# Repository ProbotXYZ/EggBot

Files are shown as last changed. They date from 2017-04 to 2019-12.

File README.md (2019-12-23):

# Egg Painter Mini (eggbot pro MOD)

<p align="center">
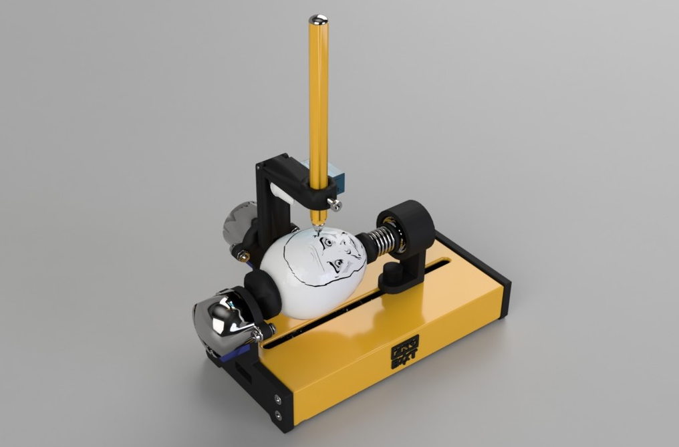
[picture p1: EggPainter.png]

<div align="center"><i>This is a low-cost version of <a href="http://egg-bot.com/">EggBot</a>, printable 3D printers that accept large.</i></div>
</p>  

<a href="https://github.com/ProbotXYZ/EggBot/blob/master/README_RU.md">На Русском</a>

Links
-------------------
<a href="https://www.youtube.com/watch?v=U3JV1u7KEp0"  target="_blank">Video Assembly Instruction</a><br/>
<a href="https://youtu.be/MZZwDX_0e_o"  target="_blank">Video First Launch</a><br/>
<a href="http://www.thingiverse.com/thing:2245428" target="_blank">Thingiverse.com</a><br/>
<a href="http://probot.xyz" target="_blank">Probot.XYZ</a><br/>
<a href="http://egg-bot.com/" target="_blank">Original EggBot</a>

Assembly kits
-------------------
You can buy a complete assembly kit - <a href="http://canbemake.ru/recommends/complete-assembly-kit/">this</a>.

Read this, it's important!
-------------------

If you are reading this, then you may be looking at the development version of EggBot Pro Mini. This means files may present inconsistencies (dimensions mismatch, lack of tolerances, etc). If you just want to build the machine, take a look at the following locations - <a href="https://github.com/ProbotXYZ/EggBot/releases">Releases</a>

The list of parts to print
-------------------
<p align="center">
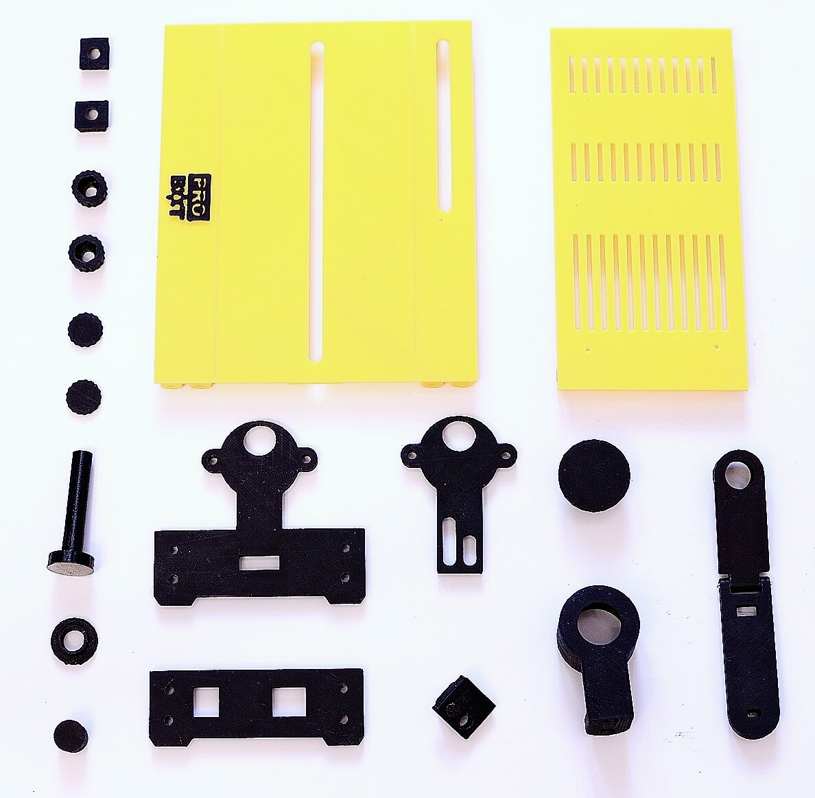
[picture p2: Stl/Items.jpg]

</p>  
1 x 0000001. Case_Bottom<br/>
1 x 0000002. Case_Top<br/>
1 x 0000003. Logo<br/>
2 x 0000004. M4_Nut_Holder<br/>
1 x 0000005. Axis_R<br/>
1 x 0000006. Spring_Holder<br/>
1 x 0000007. Axis_R_Holder<br/>
1 x 0000008. Axis_R_Lock<br/>
2 x 0000009. М4_Bolt_Holder_Bottom<br/>
2 x 0000010. М4_Bolt_Holder_Top<br/>
1 x 0000011. Axis_L_Holder<br/>
1 x 0000012. Axis_L<br/>
1 x 0000013. Hand_Holder<br/>
1 x 0000014. Hand_Holder_Guide<br/>
1 x 0000015. Hand_Holder_Guide_Case<br/>
1 x 0000016. Hand_H<br/>
1 x 0000017. Hand_V<br/>
1 x 0000018. Case_Right<br/>
<br/> 
Download and print all parts - <a href="https://github.com/ProbotXYZ/EggBot/tree/master/Stl/en">this</a><br/> or buy - <a href="http://canbemake.ru/recommends/plastic-parts-ebay/">this</a>.

Non-printable parts
-------------------
2 x <a href="http://canbemake.ru/recommends/608zz-podshipnik/" target="_blank">608zz Bearing</a><br/>
1 x <a href="http://canbemake.ru/recommends/rubber-gasket/" target="_blank">24mm Silicone or Rubber Gasket</a><br/>
1 x <a href="http://canbemake.ru/recommends/rubber-gasket/" target="_blank">15mm Silicone or Rubber Gasket</a><br/>

Screws&Nuts
-------------------
1 x <a href="http://canbemake.ru/recommends/pruzhiny/" target="_blank">Spring Diameter 9-15mm Length 17-20mm</a><br/>
1 x 2x18mm Iron Nail without a hat or <a href="http://canbemake.ru/recommends/zaklepka/" target="_blank">Rivet</a><br/>
2 x <a href="http://canbemake.ru/recommends/m5x20/" target="_blank">M5x20 Bolt</a><br/>
2 x <a href="http://canbemake.ru/recommends/m5-nut/" target="_blank">M5 Nut</a><br/>
8 x <a href="http://canbemake.ru/recommends/komplekt-boltov-m3/" target="_blank">M3x12 Screw</a><br/>
5 x <a href="http://canbemake.ru/recommends/komplekt-boltov-m3/" target="_blank">M3x16 Screw</a><br/>
12 x <a href="http://canbemake.ru/recommends/komplekt-boltov-m3/" target="_blank">M3 Nut</a><br/>
4 x <a href="http://canbemake.ru/recommends/komplekt-boltov-m3/" target="_blank">M3 Washer</a><br/>
12 x <a href="http://canbemake.ru/recommends/m2x4/" target="_blank">M2x4 or M2x5 Screw</a><br/>

Electronics
-------------------
1 x <a href="http://canbemake.ru/recommends/arduino-uno/" target="_blank">Arduino UNO</a><br/>
2 x <a href="http://canbemake.ru/recommends/uln2003-drajver-shagovogo-dvigatelya/" target="_blank">ULN2003 Stepper Motor Driver Board</a><br/>
2 x <a href="http://canbemake.ru/recommends/28byj-48-12v-shagovyj-dvigatel/" target="_blank">28byj-48-12v Stepper Motor</a><br/>
1 x <a href="http://canbemake.ru/recommends/sg90-mikro-servo-dvigatel/" target="_blank">SG90 Micro Servo</a><br/>
1 x <a href="http://canbemake.ru/recommends/12v-blok-pitaniya/" target="_blank">12V DC Power Supply</a><br/>
1 x <a href="http://canbemake.ru/recommends/usb-kabel-dlya-pk/" target="_blank">USB Cable for connect to PC</a><br/>
<a href="http://canbemake.ru/recommends/nemnogo-provodov/" target="_blank">A few wires</a><br/>

Assembly Instructions
-------------------
<a href="https://www.youtube.com/watch?v=U3JV1u7KEp0"  target="_blank">Video Assembly Instructions</a>.<br/>
Download Assembly Instructions PDF<a href="https://github.com/ProbotXYZ/EggBot/blob/master/AssemblyInstructions/Assembly_Instruction.pdf">this</a>.<br/>
3D model <a href="https://github.com/ProbotXYZ/EggBot/blob/master/AssemblyInstructions/Instruction%203D.stl">this</a>.

<p align="center">
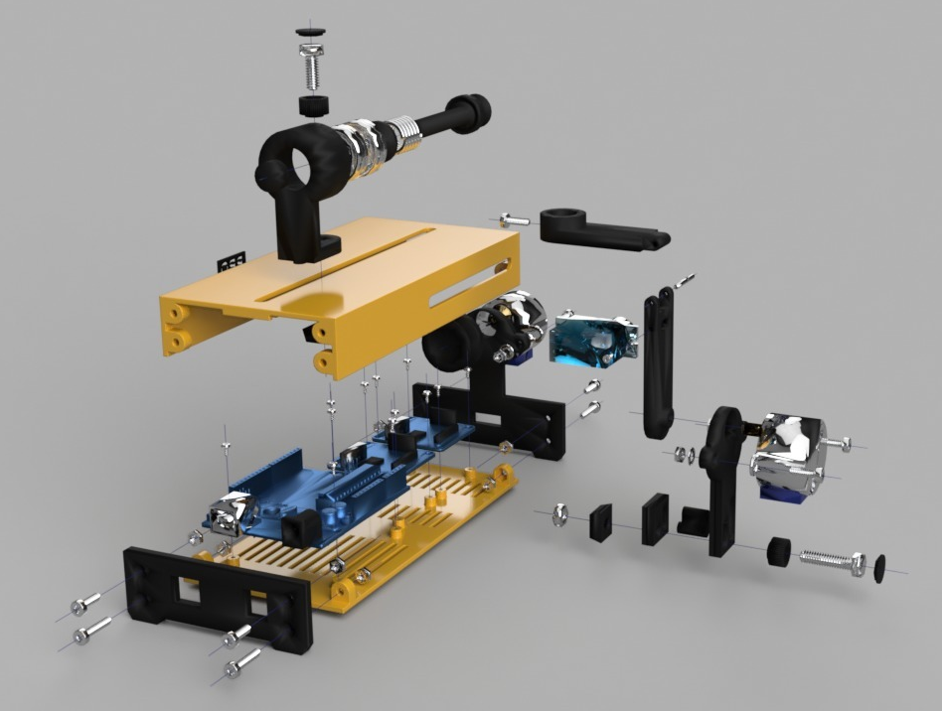
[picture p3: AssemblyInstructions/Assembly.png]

</p>  

Firmware
-------------------
As the firmware used Eggduino. It's arduino firmware for EggBot / Spherebot with Inkscape-Integration (<a href="https://github.com/cocktailyogi/EggDuino">Github</a>).

For Installation:
1) Download and unzip <a href="https://github.com/ProbotXYZ/EggBot/blob/master/Firmware/Firmware.zip">Firmware.zip</a>.
2) For UNO board with CH340G download and install driver: http://www.wch.cn/download/CH341SER_ZIP.html.
3) Download the ARDUINO IDE here: https://www.arduino.cc/en/Main/Software and install it.
4) Run the software. Select the Arduino UNO board and the proper COM PORT (should be COM5 or so) in the menu "Tools->Board"…
5) Open Eggduino.ino from <a href="https://github.com/ProbotXYZ/EggBot/blob/master/Firmware/Firmware.zip">Firmware.zip</a> and upload the Eggduino code to your Arudino Uno. 

Controlling program
-------------------
As the controlling program used Inkscape software.
1) Download and unzip the Inkscape software <a href="https://github.com/ProbotXYZ/EggBot/blob/master/Software/Software_(inkscape%2Bextension).zip">Software_inkscape+extension.zip</a>.
2) EggBot Control Extension already included in the Inkscape from <a href="https://github.com/ProbotXYZ/EggBot/blob/master/Software/Software_(inkscape%2Bextension).zip">Software_inkscape+extension.zip</a>.
3) Run the software. 

The EggBot Control extension for Inkscape is the tool that you will use to help you test and align the EggBot, as well as transfer your drawings to an egg. Once Inkscape is running, you’ll have an Extensions menu, and on that menu will be a submenu labeled Eggbot.

If the Inkscape does not connect to the device, please check name of your Arduino in to device manager. And change it in ebb_serial.py on line 52 instead of "USB-SERIAL CH340":

- open file "ebb_serial.py" in text editor and search for the following block:

    EBBport = None
    for port in comPortsList:
        if port[1].startswith("EiBotBoard"):
            EBBport = port[0]   #Success; EBB found by name match.
            break   #stop searching-- we are done.
    if EBBport is None:
        for port in comPortsList:
            if port[2].startswith("USB VID:PID=04D8:FD92"):
                EBBport = port[0] #Success; EBB found by VID/PID match.
                break   #stop searching-- we are done.      

- replace "04D8:FD92" with the VID/PID of your Arduino device.  

- alternatively, you can replace "EBBport = None" with your specific port number:
    EBBport = "COMxx"               #Windows
    EBBport = "/dev/tty[something]" #Linux/Mac  

Use template EggBot (File->New from Template) for your drawing.

Examples
-------------------
<a href="https://github.com/ProbotXYZ/EggBot/tree/master/Samples">Sample pictures</a>

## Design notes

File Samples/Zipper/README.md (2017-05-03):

# zipper template for eggbot
by schuetzi99

<p align="center">
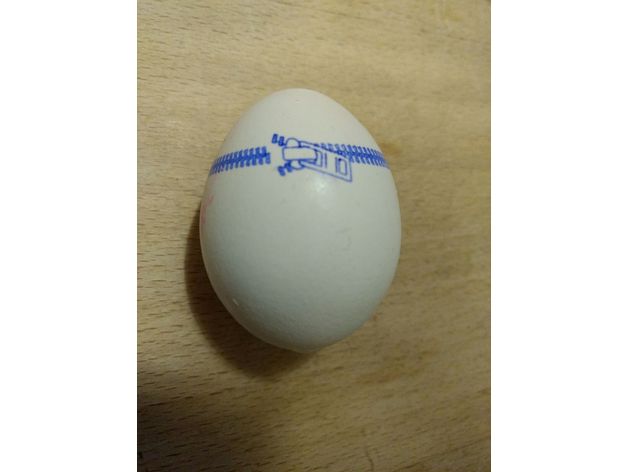
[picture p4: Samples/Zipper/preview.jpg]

</p>

http://www.thingiverse.com/thing:1981701

Summary

This is a template to print an zipper onto a egg.
https://youtu.be/jIhRP3eUceU

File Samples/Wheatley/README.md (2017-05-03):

# Eggbot - Wheatley
by R0b0Genius

http://www.thingiverse.com/thing:84653

Summary

Designed for The Original Egg-Bot Kit.
Colors are Sharpie Ultra Fine unless otherwise noted.

5 Color-Layer Plot
1: Turquoise
2: Navy Blue
3: Slate Gray
4: Black
5: Black (Martha Stewart .1mm)

www.egg-bot.com
www.evilmadscientist.com

Wheatley A© Valve Corporation

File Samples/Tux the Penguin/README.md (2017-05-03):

# Eggbot - Tux the Penguin
by R0b0Genius

<p align="center">
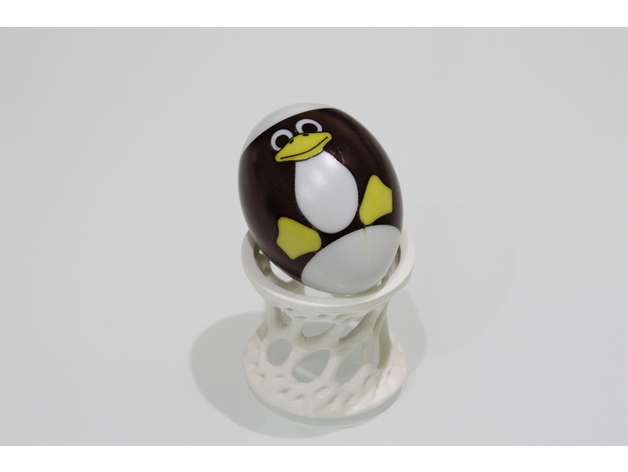
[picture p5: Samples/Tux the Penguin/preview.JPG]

</p>

http://www.thingiverse.com/thing:86924

Summary

Designed for The Original Egg-Bot Kit.
Colors are Sharpie Ultra Fine unless otherwise noted.

3 Color-Layer Plot
1: Leg Warmer Yellow
2: Slate Gray
3: Black

www.egg-bot.com
www.evilmadscientist.com

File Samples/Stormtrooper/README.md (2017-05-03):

# Eggbot - Stormtrooper
by FabLabEP

<p align="center">
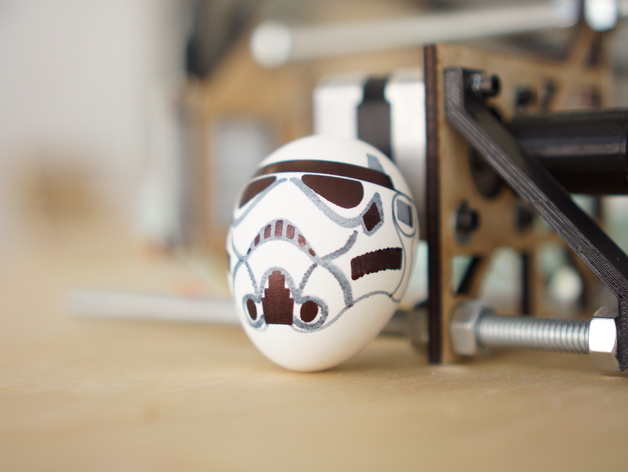
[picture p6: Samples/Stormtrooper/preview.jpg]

</p>

http://www.thingiverse.com/thing:302943

SVG file ready to print on your Eggbot.

Layers:
1: Grey
2: Black

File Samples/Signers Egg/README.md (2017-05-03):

# Signers Egg for Eggbot
by HooDat

<p align="center">
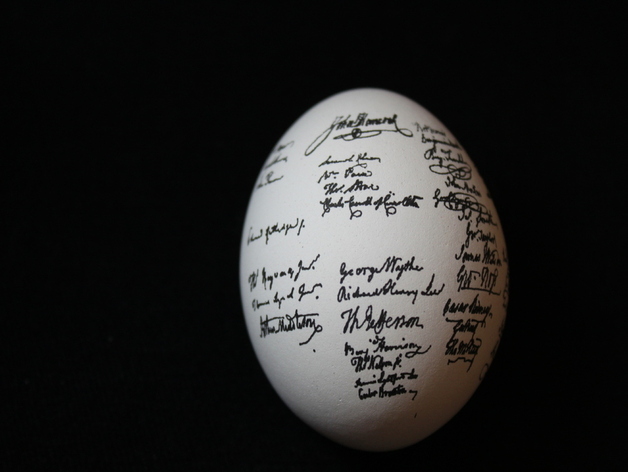
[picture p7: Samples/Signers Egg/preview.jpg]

</p>

http://www.thingiverse.com/thing:18359

Summary

Signers of the Declaration plotted with the Eggbot.
Unable to find a suitable vector based file of the Declaration, I manually traced all 56 Signers in Illustrator, saving them as smoothed paths, then imported the entire document into Inkscape. Most of them follow the pen stroke that the original Signer probably followed in 1776.

Instructions

If plotting on a normal sized egg, use as fine a point as possible. I used a 0.03mm Copic Multiliner for the pictured egg.
On larger eggs (goose, for example) it will plot OK with the .2mm Micron (size 005).

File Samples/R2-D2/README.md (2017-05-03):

# R2-D2 Eggbot Egg
by bfergus

<p align="center">
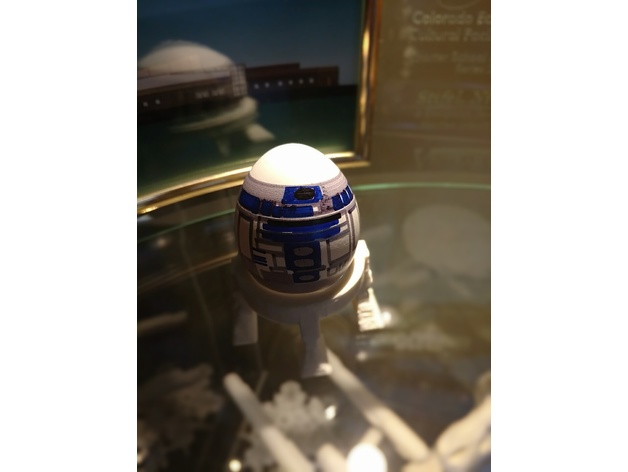
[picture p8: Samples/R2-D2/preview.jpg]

</p>

http://www.thingiverse.com/thing:2233788

Summary

Built this eggbot like this http://www.thingiverse.com/thing:299483. Making eggs. Next logical step- an egg that uses BOTH: the eggbot and printer! Here's a remixed egg stand that mimics R2D2 Legs, and an eggbot pattern for drawing an R2D2 Egg.

How I Designed This

For stand, a remix of a couple models. For the eggbot pattern, downloaded a papercraft R2D2 and converted to a multi layer svg= adding some hatching as appropriate.

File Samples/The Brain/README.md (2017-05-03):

# Eggbot - The Brain
by R0b0Genius

<p align="center">
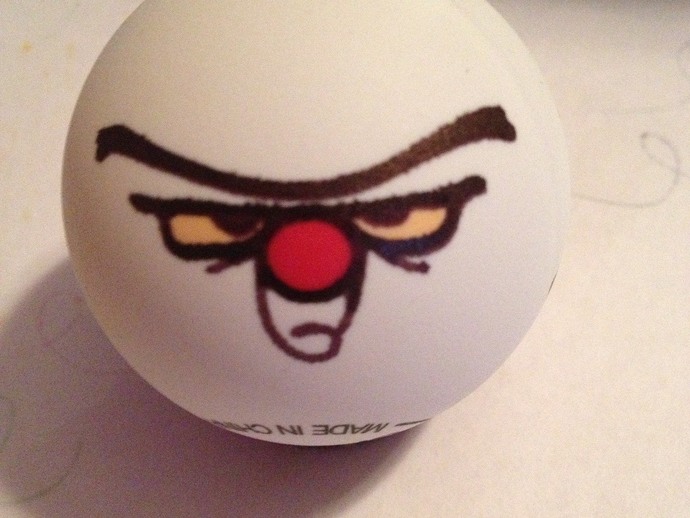
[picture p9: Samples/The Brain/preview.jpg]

</p>

http://www.thingiverse.com/thing:85200

Summary

Designed for The Original Egg-Bot Kit.
Colors are Sharpie Ultra Fine unless otherwise noted.

3 Color-Layer Plot
1: Peach
2: Red
3: Black

www.egg-bot.com
www.evilmadscientist.com

The Brain A© Warner Bros. Entertainment Inc

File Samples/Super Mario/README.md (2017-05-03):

# Super Mario Eggbot Egg
by nebarnix

<p align="center">
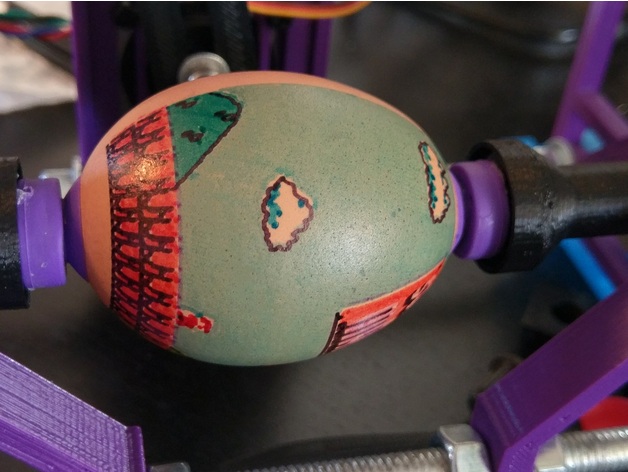
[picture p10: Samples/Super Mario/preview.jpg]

</p>

http://www.thingiverse.com/thing:2095503

Summary

The paths are somewhat messy.... Due to this it takes a while. Feel free to clean up if you have 4 hours of your life you will never get back!

Also, you should probably use a white egg, not a brown one. The sky looks a sickly grey. Maybe its just a winter inversion mario?

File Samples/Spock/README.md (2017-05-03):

# Eggbot Spock
by peterinaz

<p align="center">
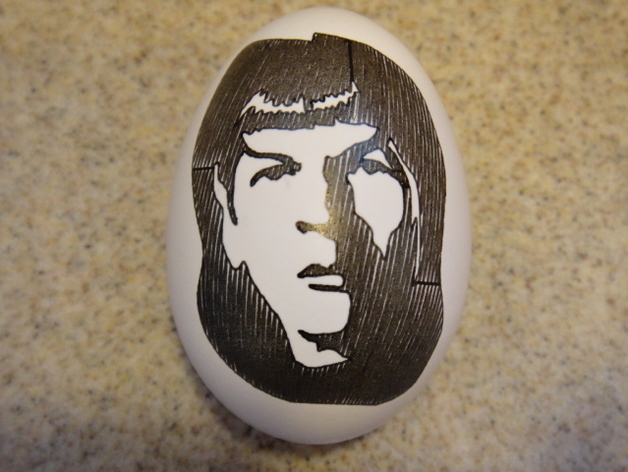
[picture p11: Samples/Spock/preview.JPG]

</p>

http://www.thingiverse.com/thing:1322623

Summary

Is there anything that really needs to be said? Done with a Sakura Pigma Micron .005 pen.

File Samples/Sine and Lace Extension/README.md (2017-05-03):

# Eggbot Sine and Lace Extension
by dnewman

<p align="center">
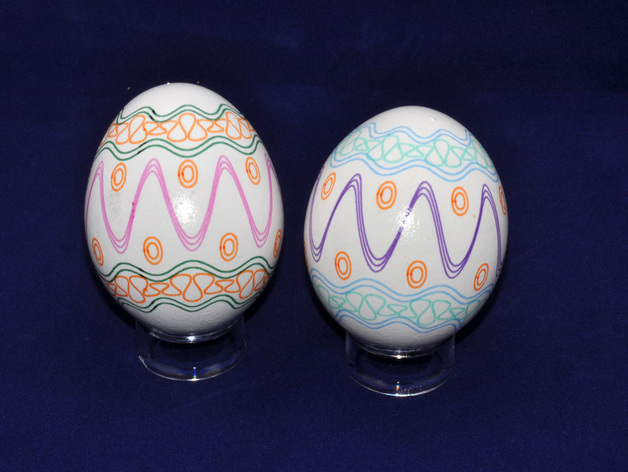
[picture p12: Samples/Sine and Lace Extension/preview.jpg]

</p>

http://www.thingiverse.com/thing:24594

Summary

Sine and Lace is an Inkscape extension intended for use with the Eggbot. It may be used to draw sinusoidal and lace patterns with periods a multiple of the document size. Two curves drawn with the extension may be selected and have a third curve drawn such that it is bounded by the first two curves. In short, the extension is intended for generating some fun patterns for drawing on eggs.

Instructions

Before you can use this extension, you need to download the eggbot_sineandlace.py and eggbot_sineandlace.inx files. Both of those files are contained in the eggbot_sineandlace.zip file which you can download from this page. Open the zip file and place its contents in your local Inkscape extension folder,
~/.config/inkscape/extensions/
on Linux and OS X. On Windows systems, you can place them directly in the Inkscape extension directory. For example, if Inkscape is installed in C:/Program Files/Inkscape then the extension directory will be C:/Program Files/Inkscape/share/extensions.
Once you have placed the two files in the proper directory, exit and then restart Inkscape. The extension should appear under the "Extensions > Eggbot Contributed" menu as "Sine and Lace...".
When using the extension there are eleven fields you can set
Width (pixels) should typically be set to the document's width in pixels. For an Eggbot plot, that's 3200 pixels. However, you can use whatever width you need: the curve will have that width horizontally.
Height (pixels) specifies the vertical peak to trough height of the curve.
Number of cycles (periods) controls the number of periods of the curve form to produce across the specified width.
The field "Start angle at 2 pi (n / m); n = " is used to control the starting phase (angle) of the sine or lace curve. Values of 0 and 1 for n and m = 2 are typical when generating a curve and a version of the same curve 180 degrees out of phase. See the green and blue touching sine waves in the lower half of the sample .svg file: the green one has n=0, m=2 and the blue one n=1, m=2. They were started at different starting y coordinates.
The field "Start angle at 2 pi (n / m); m = " is used to control the starting phase of the sine or lace curve. See the immediately preceding paragraph for mors details.
Recede from envelope is used to scale the amplitude of a curve being bounded by two other curves. The amplitude will be reduced by the specified percentage. This helps alleviate visual issues caused be imprecise pen positioning (slippage) during plotting. For a value of 100, the curve is drawn full (100%) amplitude. For a value of 5%, it will be drawn only 95% of it's full size; i.e., multiplied by a scaling factor of 0.95.
Number of sample points specifies how many points along the curve to sample. In order to get good results, this value needs to be fairly high when drawing lace and the "Spline" check box is checked.
Starting x coordinate (pixels) specifies exactly that: the horizontal page position to begin the curve at.
Starting y coordinate (pixels) is the starting page vertical position to begin the curve at. Keep in mind that with SVG and Inkscape, y=0 is at the top of the document and increasing y values move down towards the document's bottom.
To draw lace, check the "Lace" checkbox. When unchecked, a sine wave is drawn.
To generate a sequence of splines rather than straight line segments, check the "Spline" checkbox. When using splines and drawing lace, the number of sample points needs to be large.
To bound a curve by two previously drawn curves, select the two bounding curves and then select Extensions > Eggbot Contributed > Sine and Lace.... You cannot use a curve which itself was bound by two other curves.

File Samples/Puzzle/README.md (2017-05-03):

# Eggbot Puzzle
by aevictory

<p align="center">
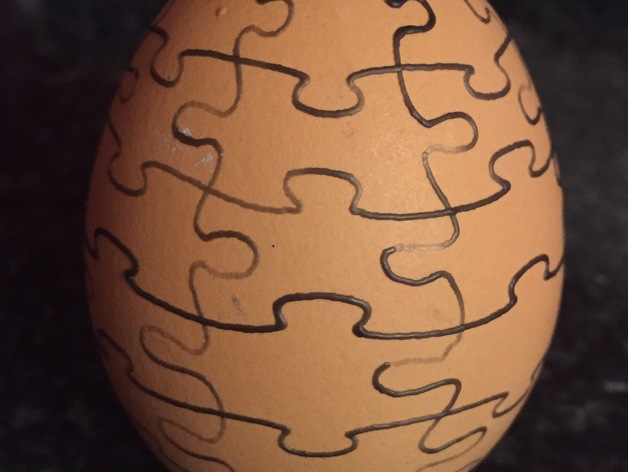
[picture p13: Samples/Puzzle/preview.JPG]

</p>

http://www.thingiverse.com/thing:660635

Summary

An Inkscape file for the Eggbot to make a puzzle.

http://shop.evilmadscientist.com/index.php

Instructions

Used homemade electric kistka. Pic is of undyed egg.

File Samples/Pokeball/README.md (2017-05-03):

# Eggbot - Pokeball
by R0b0Genius

<p align="center">
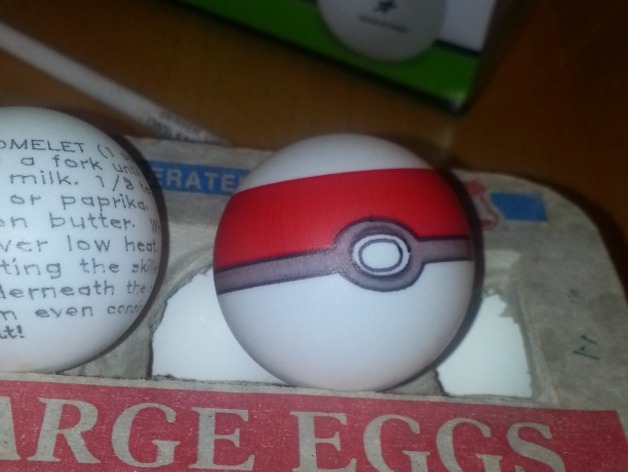
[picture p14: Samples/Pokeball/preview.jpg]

</p>

http://www.thingiverse.com/thing:84656

Summary

Designed for The Original Egg-Bot Kit.
Colors are Sharpie Ultra Fine unless otherwise noted.

3 Color-Layer Plot
1: Red
2: Slate Gray
3: Black

www.egg-bot.com
www.evilmadscientist.com

Pokeball A© PokA©mon/Nintendo

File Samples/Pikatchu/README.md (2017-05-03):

# Eggbot Pikatchu
by McOlf

<p align="center">
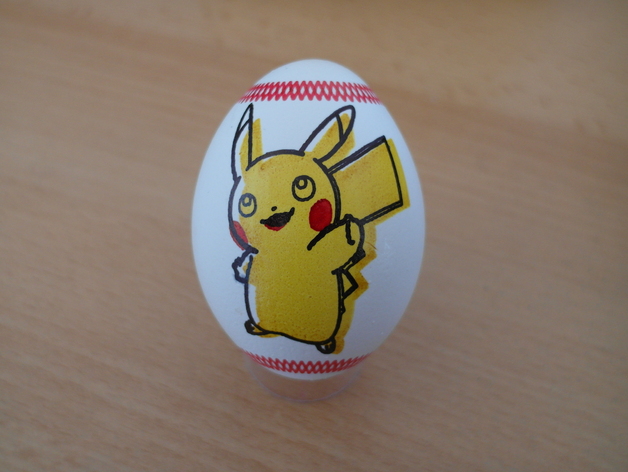
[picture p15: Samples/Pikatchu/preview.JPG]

</p>

http://www.thingiverse.com/thing:760829

Summary

Eggbot plot with Pikatchu and a rabbit.

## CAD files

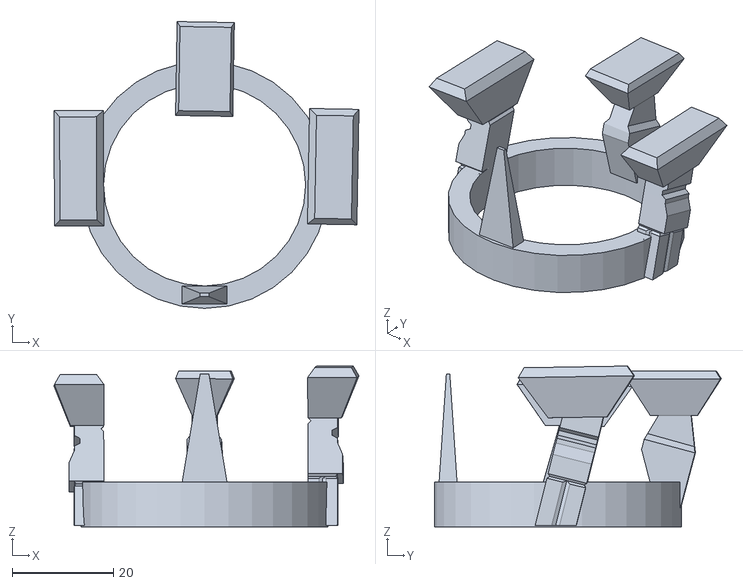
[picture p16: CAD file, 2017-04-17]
Samples/R2-D2/r2d2legs3.stl
60.1 x 56.5 x 31.7

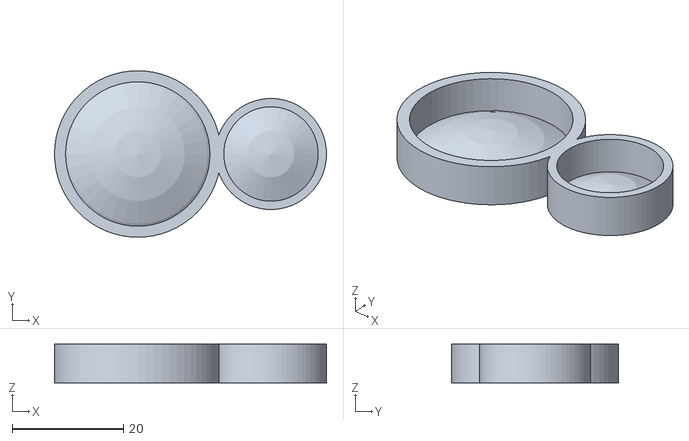
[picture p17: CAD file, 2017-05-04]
Stl/ru/Additional/Форма для отливки крепежа яйца из силикона.stl
49.0 x 30.0 x 7.00

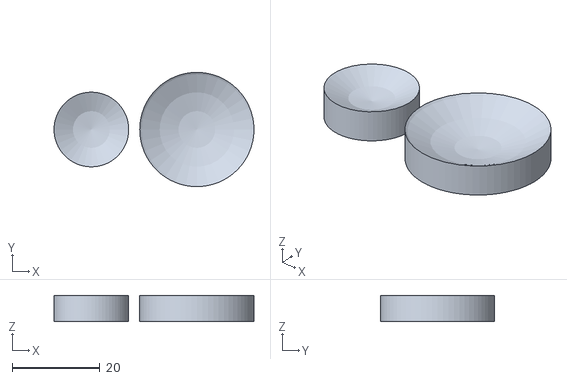
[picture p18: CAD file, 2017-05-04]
Stl/ru/Additional/Крепеж яйца для печати резиной.stl
45.5 x 26.0 x 6.00

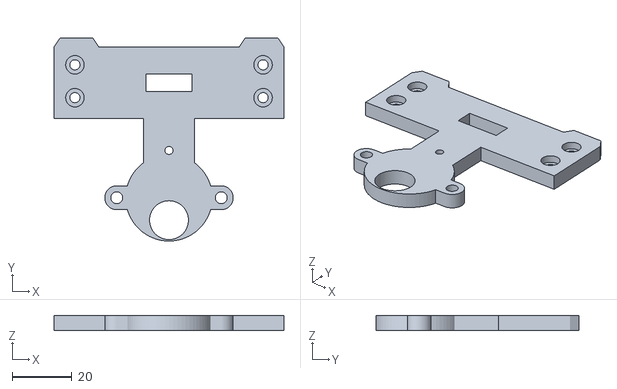
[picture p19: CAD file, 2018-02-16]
Stl/en/0000011.Axis L Holder.stl
77.0 x 68.0 x 5.00

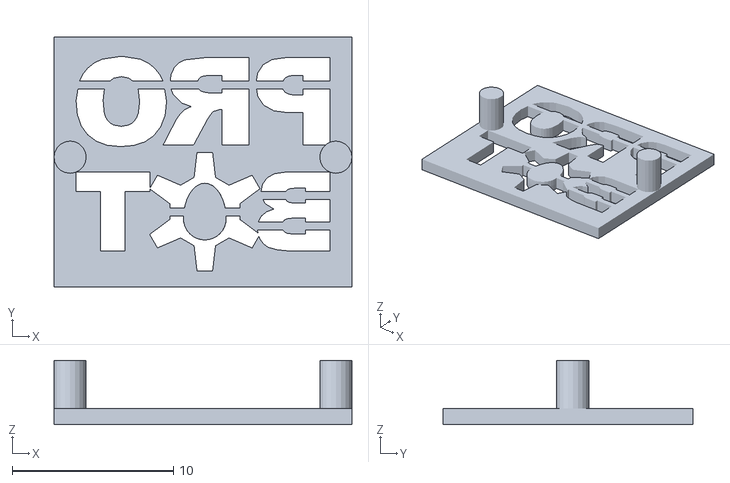
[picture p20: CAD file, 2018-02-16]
Stl/ru/0000003. Логотип.stl
18.5 x 15.5 x 4.00

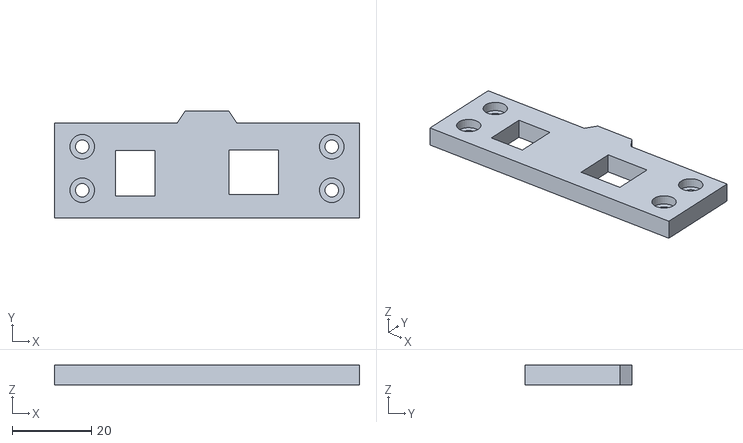
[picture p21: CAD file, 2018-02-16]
Stl/en/0000018.Case Right.stl
77.0 x 27.0 x 5.00

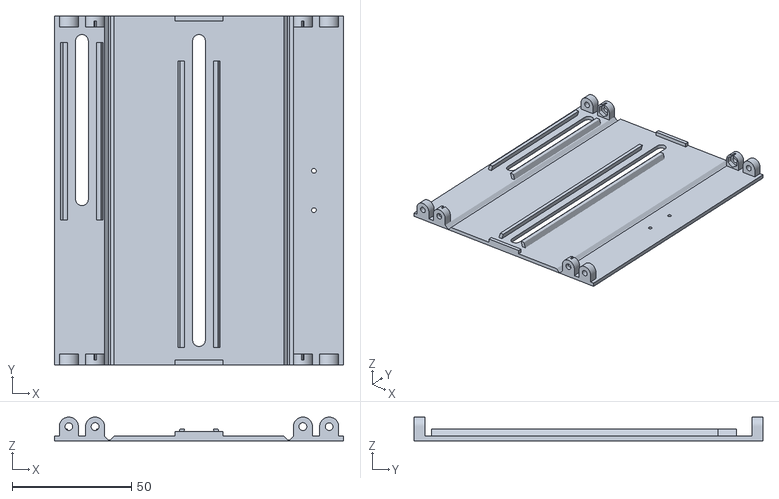
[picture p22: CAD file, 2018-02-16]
Stl/ru/0000002. Верхняя крышка корпуса.stl
121.0 x 146.0 x 10.0

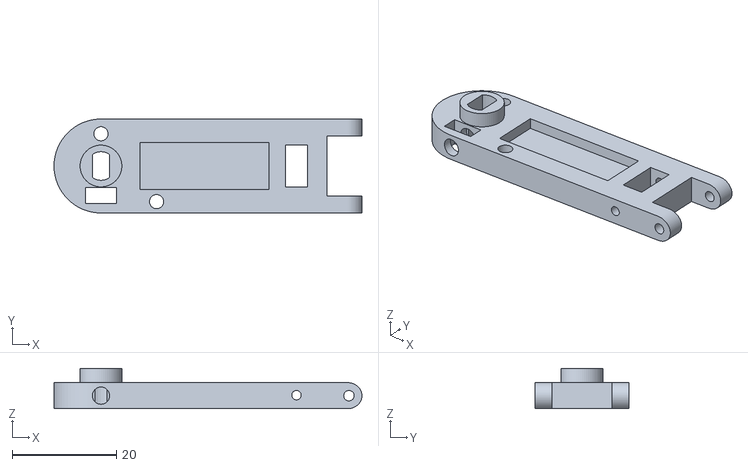
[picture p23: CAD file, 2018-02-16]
Stl/ru/0000017. Рука маркера V.stl
59.0 x 18.0 x 7.75

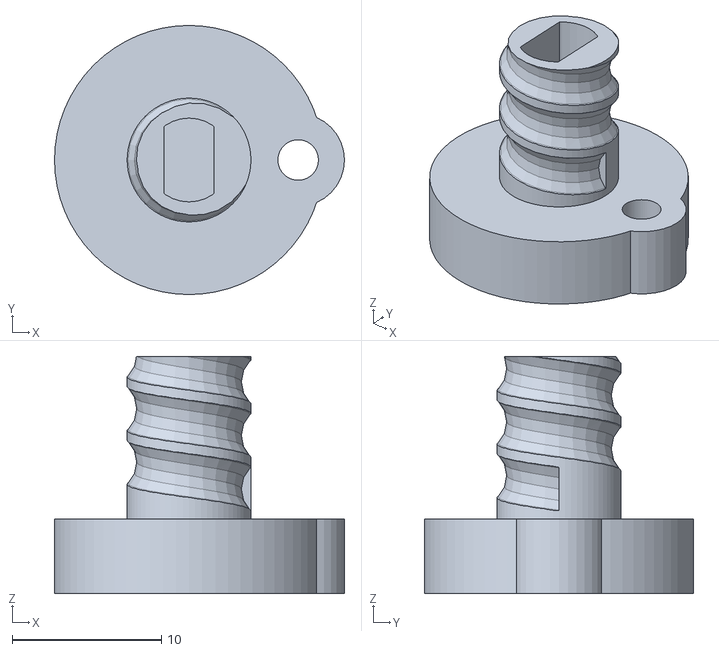
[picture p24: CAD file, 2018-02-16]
Stl/en/0000012.Axis L.stl
19.4 x 18.0 x 15.9

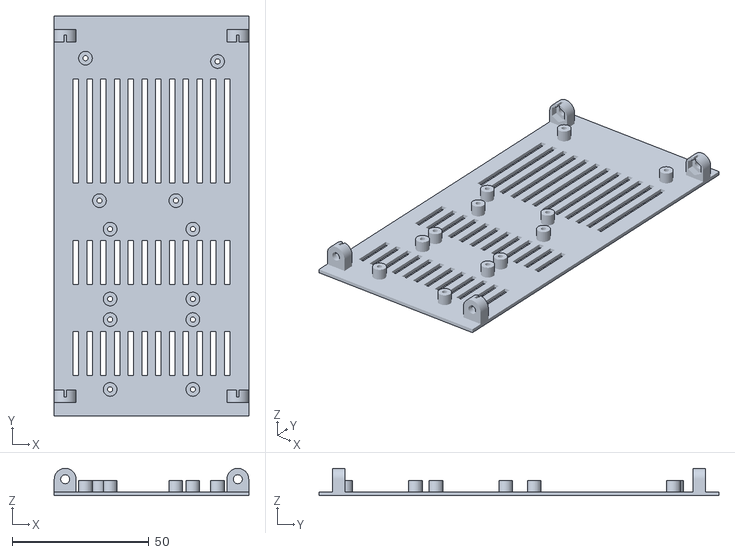
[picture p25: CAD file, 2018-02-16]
Stl/ru/0000001. Нижняя крышка корпуса.stl
71.0 x 146.0 x 10.0

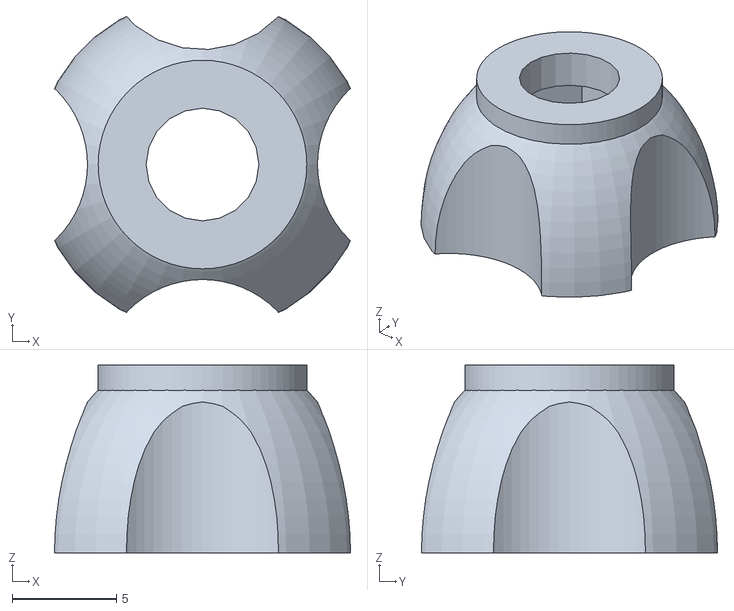
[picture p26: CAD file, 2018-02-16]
Stl/en/0000009.М5 Bolt Holder Bottom.stl
14.2 x 14.2 x 9.00

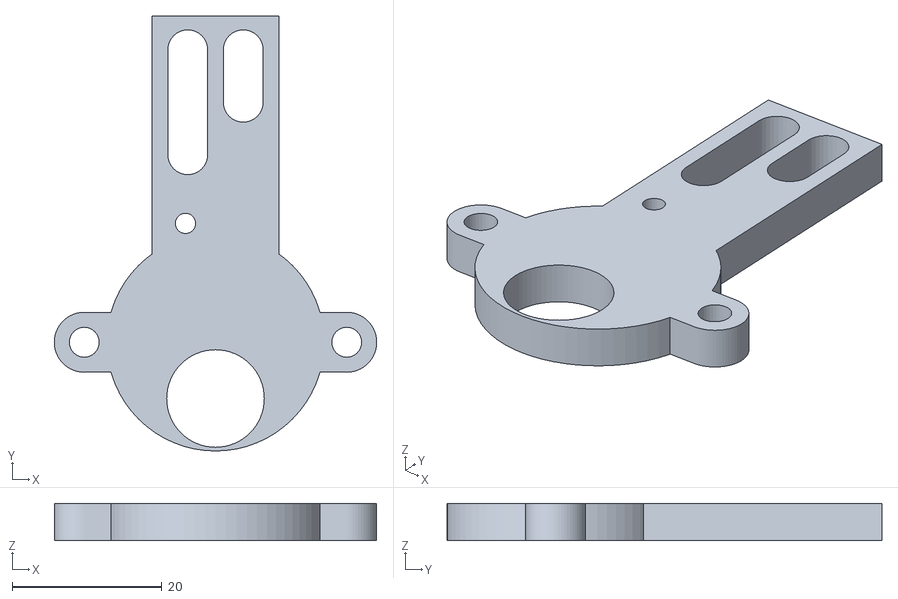
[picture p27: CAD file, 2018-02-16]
Stl/en/0000013.Hand Holder.stl
43.0 x 58.0 x 5.00

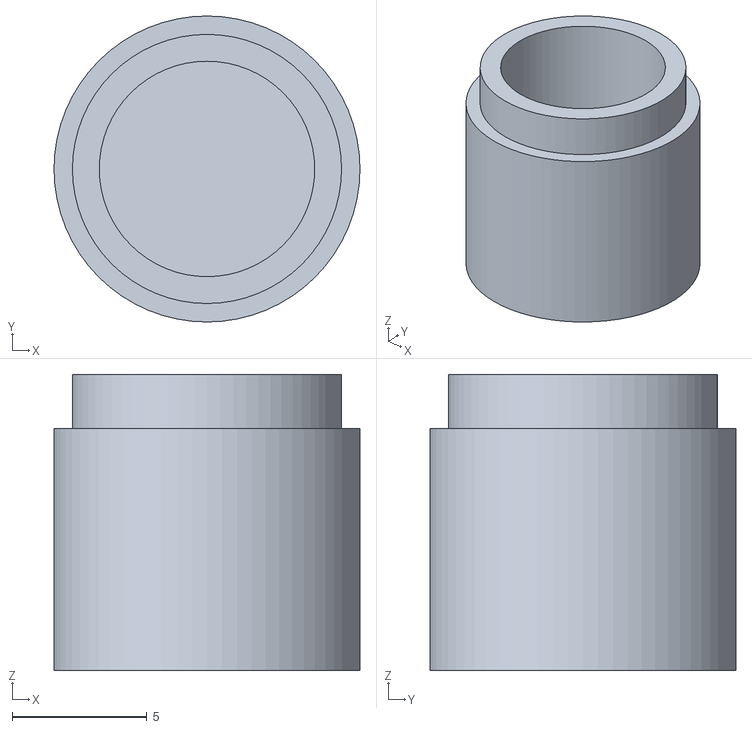
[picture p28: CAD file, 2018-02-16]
Stl/ru/0000008. Фиксатор оси поддержки.stl
11.4 x 11.4 x 11.0

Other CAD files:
Stl/en/0000002.Case Top.stl
Stl/en/0000008.Axis R Lock.stl
Stl/en/0000001.Case Bottom.stl
Stl/en/0000004.M5 Nut Holder.stl
Stl/en/0000005.Axis R.stl
Stl/en/0000006.Spring Holder.stl
Stl/en/0000007.Axis R Holder.stl
Stl/en/0000010.М5 Bolt Holder Top.stl
Stl/en/0000014.Hand Holder Guide.stl
Stl/en/0000015.Hand Holder Guide case.stl
Stl/en/0000016.Hand H.stl
Stl/ru/0000004. Держатель гайки М5.stl
Stl/ru/0000005. Правая ось поддержки яйца.stl
Stl/ru/0000006. Держатель пружины.stl
Stl/ru/0000007. Держатель правой оси.stl
Stl/ru/0000009. Держатель болта М5 низ.stl
Stl/ru/0000010. Держатель болта М5 верх.stl
Stl/ru/0000011. Держатель левой оси.stl
Stl/ru/0000014. Направляющая держателя руки маркера.stl
Stl/ru/0000015. Корпус направляющей.stl
Stl/ru/0000016. Рука маркера H.stl

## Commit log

2017-04-22 Update stl
    [0000001. Нижняя крышка корпуса.stl, 0000001.Case Bottom.stl, 0000002. Верхняя крышка корпуса.stl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]
2017-04-23 Bug fixed
    [0000006. Держатель пружины.stl, 0000006.Spring Holder.stl]
2017-04-24 Case update
    [0000001. Нижняя крышка корпуса.stl, 0000001.Case Bottom.stl]
2018-02-16 // v 1.7
    [0000001. Нижняя крышка корпуса.stl, 0000001.Case Bottom.stl, 0000002. Верхняя крышка корпуса.stl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]
